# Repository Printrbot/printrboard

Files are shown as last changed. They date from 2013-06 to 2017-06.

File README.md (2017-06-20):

printrboard
===========

Reprap Electronics for the Printrbot

For more info see the Reprap wiki page http://reprap.org/wiki/Printrboard

The BoM with Digikey P/N's is available here: https://goo.gl/G4QnvK

This project, and all of its design files (including the layout), is licensed under the [Creative Commons Attribution-ShareAlike 3.0 Unported](http://creativecommons.org/licenses/by-sa/3.0/) license.

Anyone found to be in violation of this license may not produce or discribute any products using these designs, and will have legal action taken against them.

If you do end up producing boards commercially, a donation of 5% of the retail price or $4 per board would greatly be appreciated. Paypal (lwalkera at ieee.org), or bitcoin 1Cy1JwPiEEVS1RYxfHHFcmJMKbFNrb1Nqd work the best.

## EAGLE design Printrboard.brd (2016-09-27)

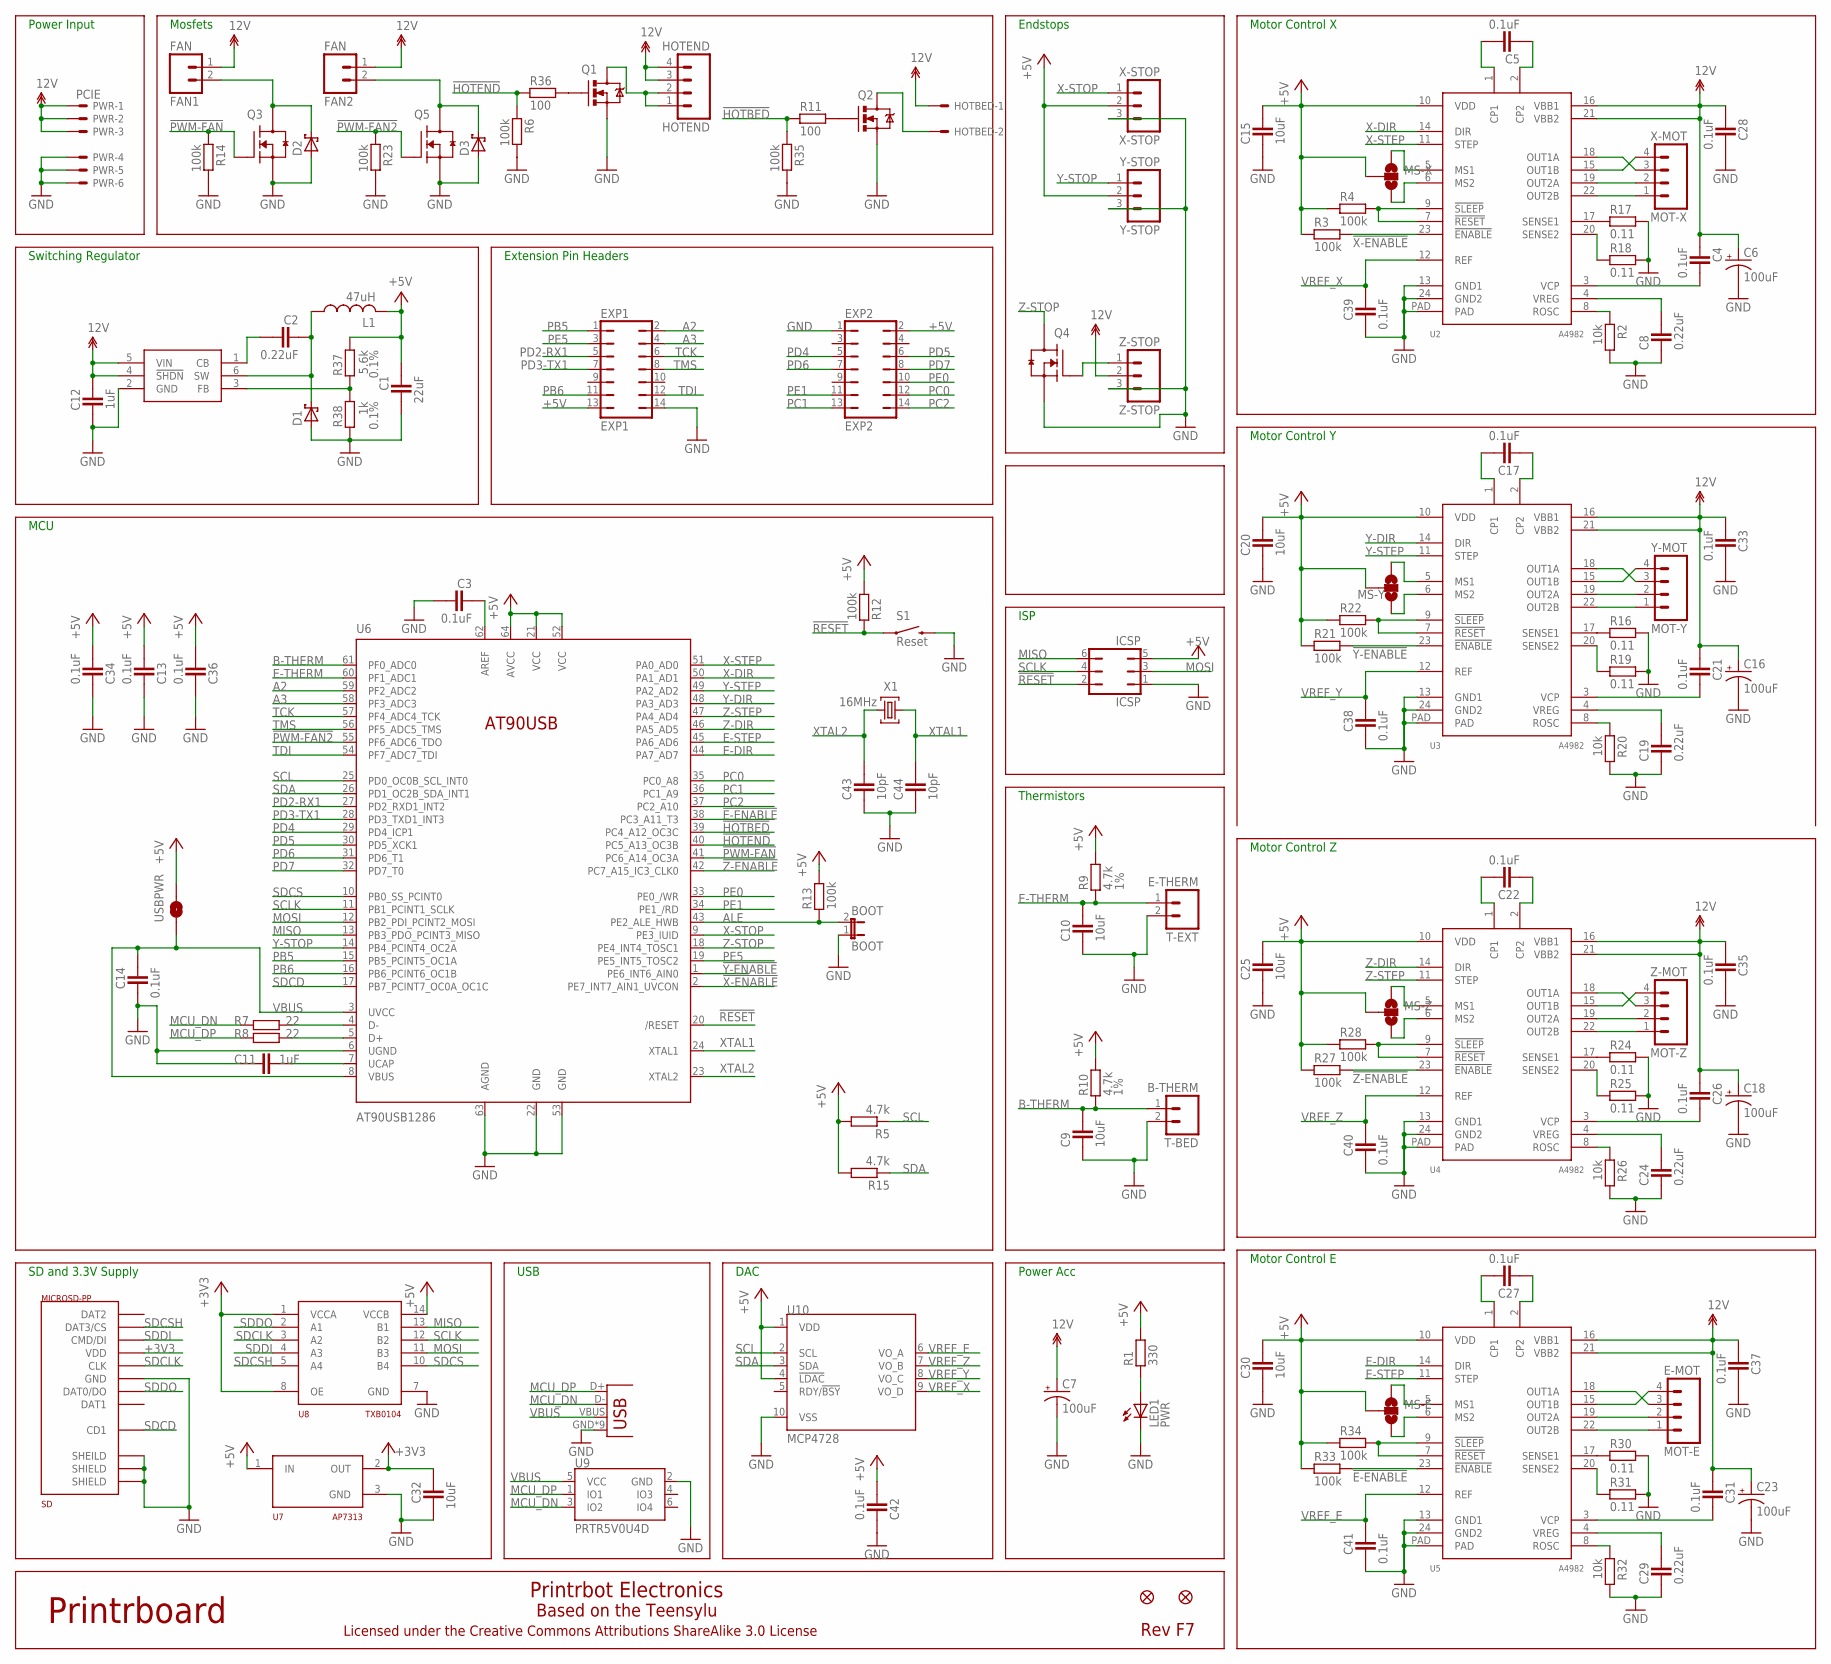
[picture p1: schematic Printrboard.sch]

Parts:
BOOT: BOOT; 1X02
C1: 22uF; CAPC2012X145AN
C2, C8, C19, C24, C29: 0.22uF; CAPC2012X145AN
C3, C4, C5, C13, C14, C17, C21, C22, C26, C27, C28, C31, C33, C34, C35, C36, C37, C38, C39, C40, C41, C42: 0.1uF; CAPC2012X145AN
C6, C7, C16, C18, C23: 100uF; PANASONIC_D
C9, C10, C15, C20, C25, C30, C32: 10uF; CAPC2012X145AN
C11, C12: 1uF; CAPC2012X145AN
C43, C44: 10pF; CAPC2012X145AN
D1, D2, D3: SCH-DIODESMA; SMA
E-MOT: MOT-E; MOLEX-1X4
EXP1: EXP1; JP7Q
EXP2: EXP2; JP7Q
FAN1, FAN2: FAN; 1X02
HOTBED: PHOENIX-2POS-5MM-SCREW; PHOENIX-5MM-2POS
HOTEND: HOTEND; MOLEX-1X4
ICSP: ICSP; JP3Q
JP26, JP33: FIDUCIAL1X2.5; FIDUCIAL-1X2.5
L1: 47uH; SDR1006
LED1: PWR; CHIP-LED0805
MS-E: SOLDERJUMPER_2WAYCONNECTED; SJ_3_CONNECTED
MS-X: SOLDERJUMPER_2WAYCONNECTED; SJ_3_CONNECTED
MS-Y: SOLDERJUMPER_2WAYCONNECTED; SJ_3_CONNECTED
MS-Z: SOLDERJUMPER_2WAYCONNECTED; SJ_3_CONNECTED
PWR: PCIE; 5566-6
Q1, Q2: RFP30N06LE; TO220V
Q3, Q4, Q5: RFP30N06LE; SOT95P280X135-3N
R1: 330; RESC2012X70N
R2, R20, R26, R32: 10k; RESC2012X70N
R3, R4, R6, R12, R13, R14, R21, R22, R23, R27, R28, R33, R34, R35: 100k; RESC2012X70N
R5, R15: 4.7k; RESC2012X70N
R7, R8: 22; RESC2012X70N
R9, R10: 4.7k; RESC2012X70N; TOLERANCE 1%
R11, R36: 100; RESC2012X70N
R16, R17, R18, R19, R24, R25, R30, R31: 0.11; RESC2012X70N
R37: 5.6k; RESC2012X70N; TOLERANCE 0.1%
R38: 1k; RESC2012X70N; TOLERANCE 0.1%
S1: Reset; TACTILE_SWITCH_TALL
SD: MICROSD-PP; USD-101-00660-68-6
T-BED: B-THERM; 1X02
T-EXT: E-THERM; 1X02
U1: LM2841; TSOT6
U2, U3, U4, U5: A4982; TSSOP-24
U6: AT90USB1286; TQFP64-2
U7: AP7313; SOT23C
U8: TXB0104; TSSOP14
U9: PRTR5V0U4D; SOT23-6
U10: MCP4728; MSOP10
USB-M: USB-MICRO-PTH; USB-MICROB-PTH
USBPWR: SOLDERJUMPERNO; SJ_2S-NO
X1: 16MHz; NDK-XTAL
X-MOT: MOT-X; MOLEX-1X4
X-STOP: X-STOP; MOLEX-1X3
Y-MOT: MOT-Y; MOLEX-1X4
Y-STOP: Y-STOP; MOLEX-1X3
Z-MOT: MOT-Z; MOLEX-1X4
Z-STOP: Z-STOP; MOLEX-1X3

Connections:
12V: C4.1, C6.+, C7.+, C12.1, C16.+, C18.+, C21.1, C23.+, C26.1, C28.1, C31.1, C33.1, C35.1, C37.1, FAN1.1, FAN2.1, HOTBED.P$1, HOTEND.3, HOTEND.4, PWR.1, PWR.2, PWR.3, U1.4 (!SHDN), U1.5 (VIN), U2.16 (VBB1), U2.21 (VBB2), U3.16 (VBB1), U3.21 (VBB2), U4.16 (VBB1), U4.21 (VBB2), U5.16 (VBB1), U5.21 (VBB2), Z-STOP.2
!E-ENABLE: R33.2, U5.23 (!ENABLE), U6.38 (PC3_A11_T3)
!HOTBED: R11.1, R35.1, U6.39 (PC4_A12_OC3C)
!HOTEND: R6.1, R36.1, U6.40 (PC5_A13_OC3B)
!PWM-FAN: Q3.1 (G), R14.1, U6.41 (PC6_A14_OC3A)
!PWM-FAN2: Q5.1 (G), R23.1, U6.55 (PF6_ADC6_TDO)
!RESET: ICSP.2, R12.1, S1.A2 (1), U6.20 (/RESET)
!X-ENABLE: R3.2, U2.23 (!ENABLE), U6.2 (PE7_INT7_AIN1_UVCON)
!Y-ENABLE: R21.2, U3.23 (!ENABLE), U6.1 (PE6_INT6_AIN0)
!Z-ENABLE: R27.2, U4.23 (!ENABLE), U6.42 (PC7_A15_IC3_CLK0)
+3V3: C32.1, SD.P$4 (VDD), U7.2 (OUT), U8.1 (VCCA), U8.8 (OE)
+5V: C1.1, C13.2, C15.2, C20.2, C25.2, C30.2, C34.2, C36.2, C42.2, EXP1.13, EXP2.2, ICSP.5, L1.P$2 (2), MS-E.2, MS-X.2, MS-Y.2, MS-Z.2, R1.2, R3.1, R4.1, R5.2, R9.2, R10.2, R12.2, R13.2, R15.2, R21.1, R22.1, R27.1, R28.1, R33.1, R34.1, R37.1, U2.10 (VDD), U3.10 (VDD), U4.10 (VDD), U5.10 (VDD), U6.21 (VCC), U6.52 (VCC), U6.64 (AVCC), U7.1 (IN), U8.14 (VCCB), U10.1 (VDD), U10.4 (!LDAC), USBPWR.2, X-STOP.2, Y-STOP.2
A2: EXP1.2, U6.59 (PF2_ADC2)
A3: EXP1.4, U6.58 (PF3_ADC3)
ALE: BOOT.2, R13.1, U6.43 (PE2_ALE_HWB)
AREF: C3.1, U6.62 (AREF)
B-THERM: C9.2, R10.1, T-BED.1, U6.61 (PF0_ADC0)
E-DIR: U5.14 (DIR), U6.44 (PA7_AD7)
E-STEP: U5.11 (STEP), U6.45 (PA6_AD6)
E-THERM: C10.2, R9.1, T-EXT.1, U6.60 (PF1_ADC1)
GND: BOOT.1, C1.2, C3.2, C6.-, C7.-, C8.1, C9.1, C10.1, C11.1, C12.2, C13.1, C14.2, C15.1, C16.-, C18.-, C19.1, C20.1, C23.-, C24.1, C25.1, C28.2, C29.1, C30.1, C32.2, C33.2, C34.1, C35.2, C36.1, C37.2, C38.2, C39.2, C40.2, C41.2, C42.1, C43.1, C44.1, D1.A, D2.A, D3.A, EXP1.14, EXP2.1, ICSP.1, LED1.C, PWR.4, PWR.5, PWR.6, Q1.3 (S), Q2.3 (S), Q3.2 (S), Q4.2 (S), Q5.2 (S), R2.2, R6.2, R14.2, R16.2, R17.2, R18.2, R19.2, R20.2, R23.2, R24.2, R25.2, R26.2, R30.2, R31.2, R32.2, R35.2, R38.2, S1.B2 (2), SD.GND1 (SHEILD), SD.GND2 (SHIELD), SD.GND3 (SHIELD), SD.P$6 (GND), T-BED.2, T-EXT.2, U1.2 (GND), U2.13 (GND1), U2.24 (GND2), U2.PAD, U3.13 (GND1), U3.24 (GND2), U3.PAD, U4.13 (GND1), U4.24 (GND2), U4.PAD, U5.13 (GND1), U5.24 (GND2), U5.PAD, U6.6 (UGND), U6.22 (GND), U6.53 (GND), U6.63 (AGND), U7.3 (GND), U8.7 (GND), U9.2 (GND), U10.10 (VSS), USB-M.GND, USB-M.GND1 (GND), USB-M.GND2 (GND), USB-M.GND3 (GND), USB-M.GND4 (GND), USB-M.GND5 (GND), USB-M.GND6 (GND), USB-M.GND7 (GND), USB-M.GND8 (GND), X-STOP.3, Y-STOP.3, Z-STOP.3
HOTBED-GND: HOTBED.P$2, Q2.2 (D)
HOTEND-GND: HOTEND.1, HOTEND.2, Q1.2 (D)
MCU_DN: R7.1, U9.3 (IO2), USB-M.D-
MCU_DP: R8.1, U9.1 (IO1), USB-M.D+
MISO: ICSP.6, U6.13 (PB3_PDO_PCINT3_MISO), U8.13 (B1)
MOSI: ICSP.3, U6.12 (PB2_PDI_PCINT2_MOSI), U8.11 (B3)
unnamed: LED1.A, R1.1
unnamed: D2.C, FAN1.2, Q3.3 (D)
unnamed: R7.2, U6.4 (D-)
unnamed: R8.2, U6.5 (D+)
unnamed: Q4.1 (G), Z-STOP.1
unnamed: Q2.1 (G), R11.2
unnamed: D3.C, FAN2.2, Q5.3 (D)
unnamed: C11.2, U6.7 (UCAP)
unnamed: U2.18 (OUT1A), X-MOT.3
unnamed: C5.2, U2.1 (CP1)
unnamed: C5.1, U2.2 (CP2)
unnamed: R2.1, U2.8 (ROSC)
unnamed: R17.1, U2.17 (SENSE1)
unnamed: R18.1, U2.20 (SENSE2)
unnamed: C4.2, U2.3 (VCP)
unnamed: U2.15 (OUT1B), X-MOT.4
unnamed: C8.2, U2.4 (VREG)
unnamed: U2.19 (OUT2A), X-MOT.2
unnamed: R4.2, U2.7 (!RESET), U2.9 (!SLEEP)
unnamed: R37.2, R38.1, U1.3 (FB)
unnamed: U2.22 (OUT2B), X-MOT.1
unnamed: U3.19 (OUT2A), Y-MOT.2
unnamed: U3.22 (OUT2B), Y-MOT.1
unnamed: U3.15 (OUT1B), Y-MOT.4
unnamed: MS-X.1, U2.5 (MS1)
unnamed: MS-X.3, U2.6 (MS2)
unnamed: C17.2, U3.1 (CP1)
unnamed: C17.1, U3.2 (CP2)
unnamed: U3.18 (OUT1A), Y-MOT.3
unnamed: R19.1, U3.20 (SENSE2)
unnamed: R20.1, U3.8 (ROSC)
unnamed: C19.2, U3.4 (VREG)
unnamed: R22.2, U3.7 (!RESET), U3.9 (!SLEEP)
unnamed: C21.2, U3.3 (VCP)
unnamed: R16.1, U3.17 (SENSE1)
unnamed: U4.15 (OUT1B), Z-MOT.4
unnamed: U4.18 (OUT1A), Z-MOT.3
unnamed: U4.19 (OUT2A), Z-MOT.2
unnamed: MS-Y.1, U3.5 (MS1)
unnamed: MS-Y.3, U3.6 (MS2)
unnamed: C22.2, U4.1 (CP1)
unnamed: C22.1, U4.2 (CP2)
unnamed: R24.1, U4.17 (SENSE1)
unnamed: R25.1, U4.20 (SENSE2)
unnamed: R26.1, U4.8 (ROSC)
unnamed: C24.2, U4.4 (VREG)
unnamed: R28.2, U4.7 (!RESET), U4.9 (!SLEEP)
unnamed: C26.2, U4.3 (VCP)
unnamed: U4.22 (OUT2B), Z-MOT.1
unnamed: E-MOT.4, U5.15 (OUT1B)
unnamed: E-MOT.3, U5.18 (OUT1A)
unnamed: E-MOT.2, U5.19 (OUT2A)
unnamed: MS-Z.1, U4.5 (MS1)
unnamed: MS-Z.3, U4.6 (MS2)
unnamed: C27.2, U5.1 (CP1)
unnamed: C27.1, U5.2 (CP2)
unnamed: R30.1, U5.17 (SENSE1)
unnamed: R31.1, U5.20 (SENSE2)
unnamed: R32.1, U5.8 (ROSC)
unnamed: C29.2, U5.4 (VREG)
unnamed: R34.2, U5.7 (!RESET), U5.9 (!SLEEP)
unnamed: C31.2, U5.3 (VCP)
unnamed: E-MOT.1, U5.22 (OUT2B)
unnamed: Q1.1 (G), R36.2
unnamed: MS-E.1, U5.5 (MS1)
unnamed: MS-E.3, U5.6 (MS2)
unnamed: C2.1, D1.C, L1.P$1 (1), U1.6 (SW)
unnamed: C2.2, U1.1 (CB)
PB5: EXP1.1, U6.15 (PB5_PCINT5_OC1A)
PB6: EXP1.11, U6.16 (PB6_PCINT6_OC1B)
PC0: EXP2.12, U6.35 (PC0_A8)
PC1: EXP2.13, U6.36 (PC1_A9)
PC2: EXP2.14, U6.37 (PC2_A10)
PD2-RX1: EXP1.5, U6.27 (PD2_RXD1_INT2)
PD3-TX1: EXP1.7, U6.28 (PD3_TXD1_INT3)
PD4: EXP2.5, U6.29 (PD4_ICP1)
PD5: EXP2.6, U6.30 (PD5_XCK1)
PD6: EXP2.7, U6.31 (PD6_T1)
PD7: EXP2.8, U6.32 (PD7_T0)
PE0: EXP2.10, U6.33 (PE0_/WR)
PE1: EXP2.11, U6.34 (PE1_/RD)
PE5: EXP1.3, U6.19 (PE5_INT5_TOSC2)
SCL: R5.1, U6.25 (PD0_OC0B_SCL_INT0), U10.2 (SCL)
SCLK: ICSP.4, U6.11 (PB1_PCINT1_SCLK), U8.12 (B2)
SDA: R15.1, U6.26 (PD1_OC2B_SDA_INT1), U10.3 (SDA)
SDCD: SD.CD (CD1), U6.17 (PB7_PCINT7_OC0A_OC1C)
SDCLK: SD.P$5 (CLK), U8.3 (A2)
SDCS: U6.10 (PB0_SS_PCINT0), U8.10 (B4)
SDCSH: SD.P$2 (DAT3/CS), U8.5 (A4)
SDDI: SD.P$3 (CMD/DI), U8.4 (A3)
SDDO: SD.P$7 (DAT0/DO), U8.2 (A1)
TCK: EXP1.6, U6.57 (PF4_ADC4_TCK)
TDI: EXP1.12, U6.54 (PF7_ADC7_TDI)
TMS: EXP1.8, U6.56 (PF5_ADC5_TMS)
VBUS: C14.1, U6.3 (UVCC), U6.8 (VBUS), U9.5 (VCC), USB-M.VBUS, USBPWR.1
VREF_E: C41.1, U5.12 (REF), U10.6 (VO_A)
VREF_X: C39.1, U2.12 (REF), U10.9 (VO_D)
VREF_Y: C38.1, U3.12 (REF), U10.8 (VO_C)
VREF_Z: C40.1, U4.12 (REF), U10.7 (VO_B)
X-DIR: U2.14 (DIR), U6.50 (PA1_AD1)
X-STEP: U2.11 (STEP), U6.51 (PA0_AD0)
X-STOP: U6.9 (PE3_IUID), X-STOP.1
XTAL1: C44.2, U6.24 (XTAL1), X1.P$1 (1)
XTAL2: C43.2, U6.23 (XTAL2), X1.P$2 (2)
Y-DIR: U3.14 (DIR), U6.48 (PA3_AD3)
Y-STEP: U3.11 (STEP), U6.49 (PA2_AD2)
Y-STOP: U6.14 (PB4_PCINT4_OC2A), Y-STOP.1
Z-DIR: U4.14 (DIR), U6.46 (PA5_AD5)
Z-STEP: U4.11 (STEP), U6.47 (PA4_AD4)
Z-STOP: Q4.3 (D), U6.18 (PE4_INT4_TOSC1)

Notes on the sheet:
Motor Control X
Motor Control Y
Motor Control Z
Motor Control E
ISP
Thermistors
Endstops
Mosfets
Power Acc
Printrboard
Rev F7
Printrbot Electronics
Licensed under the Creative Commons Attributions ShareAlike 3.0 License
Extension Pin Headers
Switching Regulator
Based on the Teensylu
SD and 3.3V Supply
Power Input
MCU
USB
DAC

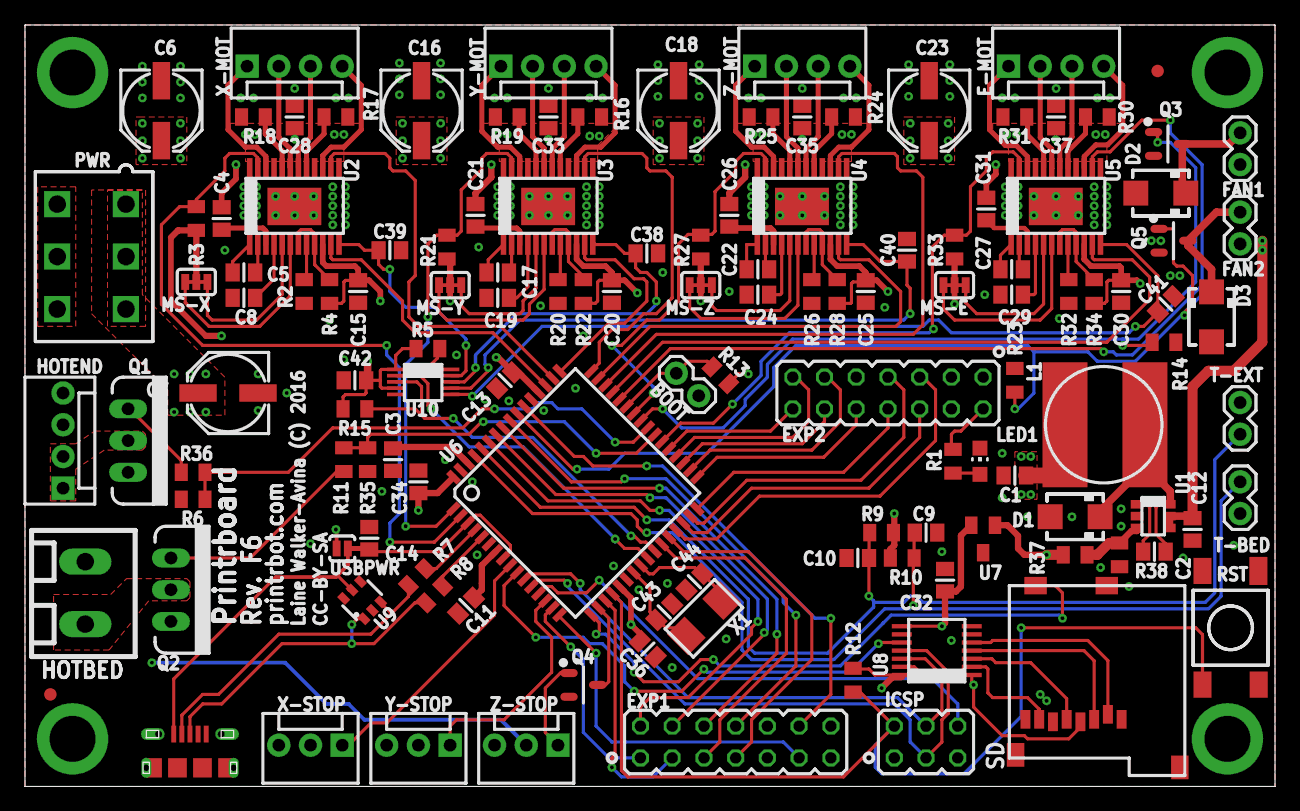
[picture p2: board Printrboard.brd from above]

Board: 4 copper layers, 100.1 x 61.0 mm, 130 parts (0 on the bottom side), 137 nets.

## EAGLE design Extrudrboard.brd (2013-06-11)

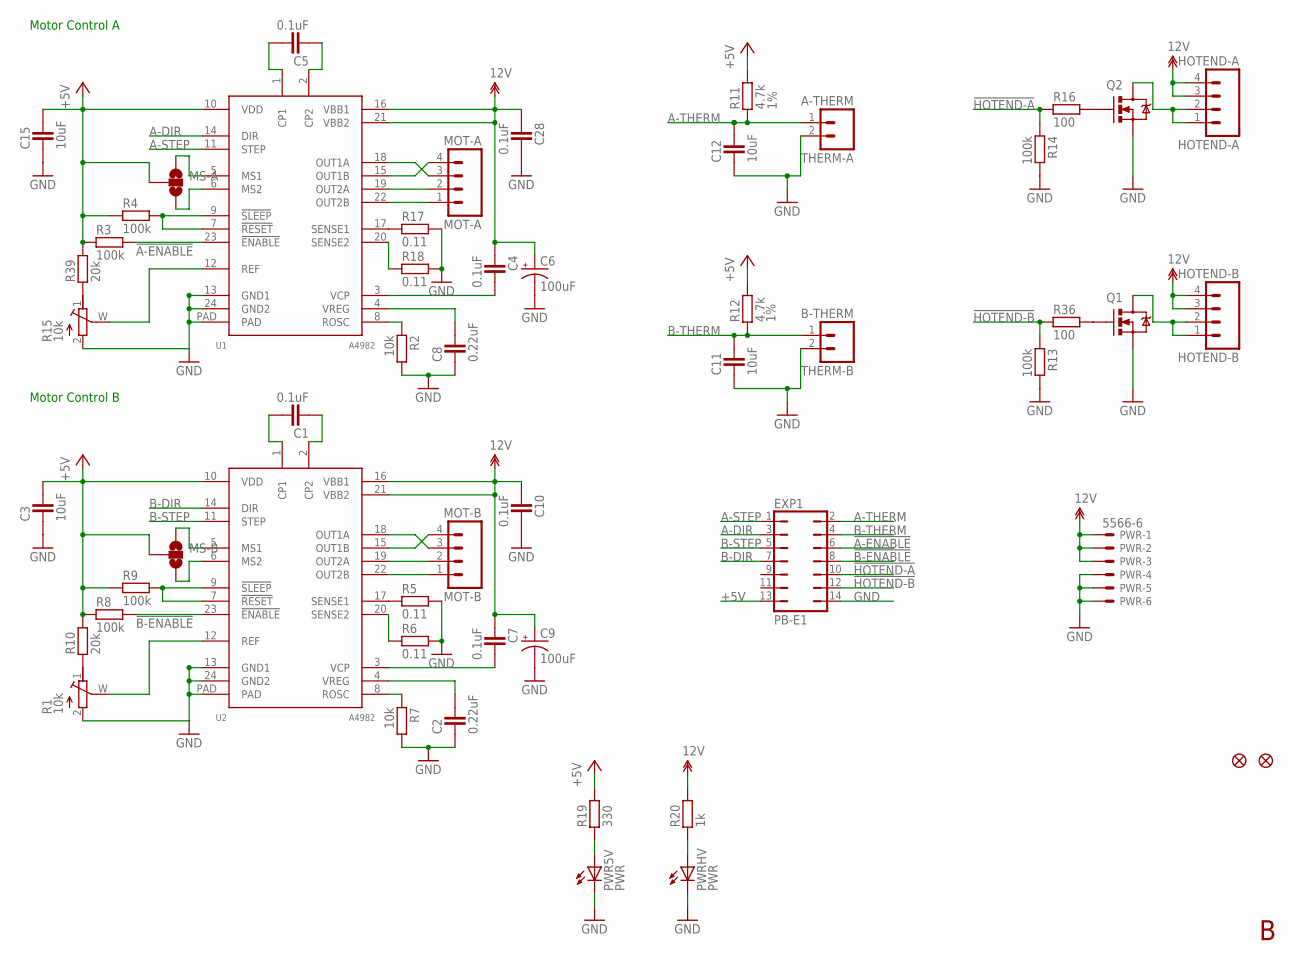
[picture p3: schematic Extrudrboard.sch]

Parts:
C1, C4, C5, C7, C10, C28: 0.1uF; CAPC2012X145AN
C2, C8: 0.22uF; CAPC2012X145AN
C3, C11, C12, C15: 10uF; CAPC2012X145AN
C6, C9: 100uF; PANASONIC_D
EXP1: PB-E1; JP7Q
HOTEND-A: HOTEND-A; MOLEX-1X4
HOTEND-B: HOTEND-B; MOLEX-1X4
JP1, JP2: FIDUCIAL1X2.5; FIDUCIAL-1X2.5
MOT-A: MOT-A; MOLEX-1X4
MOT-B: MOT-B; MOLEX-1X4
MS-A: SOLDERJUMPER_2WAYCONNECTED; SJ_3_CONNECTED
MS-B: SOLDERJUMPER_2WAYCONNECTED; SJ_3_CONNECTED
PWR: 5566-6
PWR5V: PWR; CHIP-LED0805
PWRHV: PWR; CHIP-LED0805
Q1, Q2: MOSFET-NCHANNELPTH2; TO220V
R1, R15: 10k; RTRIM-ST4ETB
R2, R7: 10k; RESC2012X70N
R3, R4, R8, R9, R13, R14: 100k; RESC2012X70N
R5, R6, R17, R18: 0.11; RESC2012X70N
R10, R39: 20k; RESC2012X70N
R11, R12: 4.7k; RESC2012X70N; TOLERANCE 1%
R16, R36: 100; RESC2012X70N
R19: 330; RESC2012X70N
R20: 1k; RESC2012X70N
THERM-A: A-THERM; 1X02
THERM-B: B-THERM; 1X02
U1, U2: A4982; TSSOP-24

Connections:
12V: C4.1, C6.+, C7.1, C9.+, C10.1, C28.1, HOTEND-A.3, HOTEND-A.4, HOTEND-B.3, HOTEND-B.4, PWR.1, PWR.2, PWR.3, R20.2, U1.16 (VBB1), U1.21 (VBB2), U2.16 (VBB1), U2.21 (VBB2)
!A-ENABLE: EXP1.6, R3.2, U1.23 (!ENABLE)
!B-ENABLE: EXP1.8, R8.2, U2.23 (!ENABLE)
!HOTEND-A: EXP1.10, R14.1, R16.1
!HOTEND-B: EXP1.12, R13.1, R36.1
+5V: C3.2, C15.2, EXP1.13, MS-A.2, MS-B.2, R3.1, R4.1, R8.1, R9.1, R10.2, R11.2, R12.2, R19.2, R39.2, U1.10 (VDD), U2.10 (VDD)
A-DIR: EXP1.3, U1.14 (DIR)
A-STEP: EXP1.1, U1.11 (STEP)
A-THERM: C12.2, EXP1.2, R11.1, THERM-A.1
B-DIR: EXP1.7, U2.14 (DIR)
B-STEP: EXP1.5, U2.11 (STEP)
B-THERM: C11.2, EXP1.4, R12.1, THERM-B.1
GND: C2.1, C3.1, C6.-, C8.1, C9.-, C10.2, C11.1, C12.1, C15.1, C28.2, EXP1.14, PWR.4, PWR.5, PWR.6, PWR5V.C, PWRHV.C, Q1.3 (S), Q2.3 (S), R1.2 (E), R2.2, R5.2, R6.2, R7.2, R13.2, R14.2, R15.2 (E), R17.2, R18.2, THERM-A.2, THERM-B.2, U1.13 (GND1), U1.24 (GND2), U1.PAD, U2.13 (GND1), U2.24 (GND2), U2.PAD
HOTENDA-GND: HOTEND-A.1, HOTEND-A.2, Q2.2 (D)
HOTENDB-GND: HOTEND-B.1, HOTEND-B.2, Q1.2 (D)
unnamed: C1.2, U2.1 (CP1)
unnamed: C1.1, U2.2 (CP2)
unnamed: R5.1, U2.17 (SENSE1)
unnamed: R6.1, U2.20 (SENSE2)
unnamed: R1.W (S), U2.12 (REF)
unnamed: R7.1, U2.8 (ROSC)
unnamed: C2.2, U2.4 (VREG)
unnamed: R9.2, U2.7 (!RESET), U2.9 (!SLEEP)
unnamed: C7.2, U2.3 (VCP)
unnamed: MOT-A.3, U1.18 (OUT1A)
unnamed: C5.2, U1.1 (CP1)
unnamed: C5.1, U1.2 (CP2)
unnamed: R2.1, U1.8 (ROSC)
unnamed: R17.1, U1.17 (SENSE1)
unnamed: R18.1, U1.20 (SENSE2)
unnamed: C4.2, U1.3 (VCP)
unnamed: MOT-A.4, U1.15 (OUT1B)
unnamed: R15.W (S), U1.12 (REF)
unnamed: C8.2, U1.4 (VREG)
unnamed: MOT-A.2, U1.19 (OUT2A)
unnamed: R4.2, U1.7 (!RESET), U1.9 (!SLEEP)
unnamed: MS-B.1, U2.5 (MS1)
unnamed: MOT-A.1, U1.22 (OUT2B)
unnamed: MS-B.3, U2.6 (MS2)
unnamed: MOT-B.3, U2.18 (OUT1A)
unnamed: MOT-B.4, U2.15 (OUT1B)
unnamed: MS-A.1, U1.5 (MS1)
unnamed: MS-A.3, U1.6 (MS2)
unnamed: MOT-B.2, U2.19 (OUT2A)
unnamed: MOT-B.1, U2.22 (OUT2B)
unnamed: R1.1 (A), R10.1
unnamed: Q2.1 (G), R16.2
unnamed: PWR5V.A, R19.1
unnamed: PWRHV.A, R20.1
unnamed: R15.1 (A), R39.1
unnamed: Q1.1 (G), R36.2

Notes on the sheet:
Motor Control A
Motor Control B

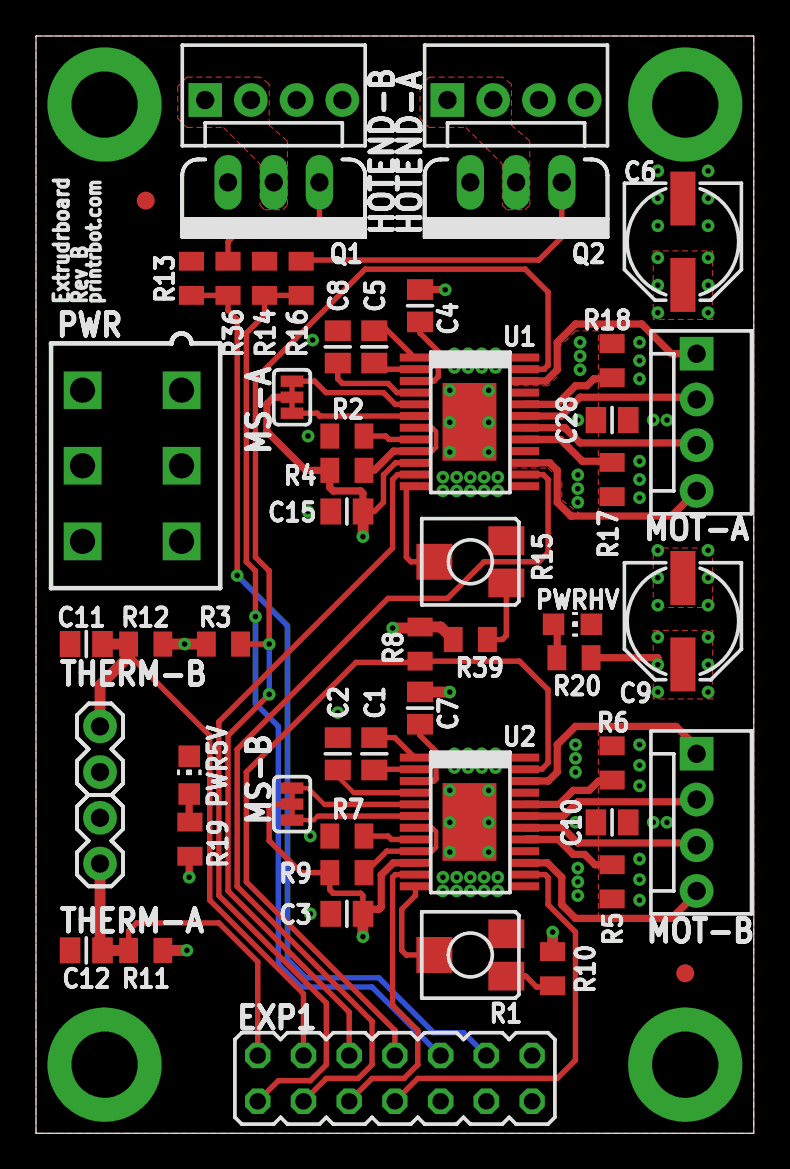
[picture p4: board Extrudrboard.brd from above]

Board: 4 copper layers, 39.9 x 61.0 mm, 54 parts (0 on the bottom side), 51 nets.

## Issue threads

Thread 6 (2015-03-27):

Add BOM to repo

jbryson3, 2015-03-27:
It would be helpful to track changes in the actual parts used. For instance, I'm looking at the current BOM for the F4 board and it shows Q4 as a BJT, where on my Printrbot F4 board, I see a FET. Not sure what changed and when, especially since the boards are the same version.

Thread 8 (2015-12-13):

Add feature to allow control of hotend fan

PxT, 2015-12-13:
It would be good to have software / firmware control of the always-on hotend fan.  Currently these are just wired to constant power on the board but a controllable pin that cuts power when the hotend is below a safe threshold would be better.  That way when a print is complete and the hotend cools completely the fan could shut off automatically, reducing noise and extending the life of the fan.

Not sure if this requires a hardware redesign or not.  Would definitely require a corresponding firmware modification.  There is precedent for this feature in Repetier firmware w/ RAMBO boards.

PxT, 2015-12-13:
Further discussion here: http://www.printrbottalk.com/forum/viewtopic.php?f=21&t=10508&p=67897&hilit=fan+mosfet#p67897

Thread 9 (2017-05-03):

Charge pump capacitors on A4982's sing

jetty840, 2017-05-03:
The charge pump 0.1uF capacitors on the CP1/CP2 pins on the A4982 sing emitting a high pitch sound which can be detected by and is irritating to younger users, approximately 12-16KHz.

The charge pump operates at 52KHz, with a superimposed waveform of approximately 6-8Khz at 8V peak to peak.  This causes the piezo material in the Y5V capacitor to emit sound due to the piezo electric effect at the fundamental and resonate at the 1st harmonic.  Frequency can vary slightly from driver to driver according to manufacturing tolerances in the A4982 charge pump circuitry.

A 14dB improvement can be achieved by replacing these 4 caps with a X7R Kemet P/N  C0805C104K1RACTU.

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

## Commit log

2011-11-23 Fix some thermal, and angle errors. Add some additional caps on Vbb rail. More work on the silkscreen
    [Printrboard.brd, Printrboard.sch]
2011-11-25 Add solder jumpers and move placement artwork for the Allegro package to tPlace
2011-11-25 Change to using solder jumpers for the microstepping selection
    [Printrboard.brd, Printrboard.sch]
2011-11-30 Change thermal vias for the stepper driver, reduce paste area on drivers to 75%, make edge clearance 20 mils, and bring Vbb ceramic cap to top side
    [Printrboard.brd, Printrboard.sch]
2011-11-30 Tweak the position of the motor traces
    [Printrboard.brd]
2011-12-03 Copy level translator and LDO from SD adapter project in prep for 5V conversion
2011-12-03 Add resistors on all the Vref pots to allow for 5V change, and cleanup the silkscreen layers
    [Printrboard.brd, Printrboard.sch]
2011-12-10 Change logic voltage to 5V, add translation circuitry for SD, move to 4-layer design, and cleanup some packages
    [Printrboard.brd, Printrboard.sch]
2011-12-11 Tweak the board to pass 4pcb.com DFM
    [Printrboard.brd]
2011-12-16 Convert files to EAGLE 6
    [Printrboard.brd, Printrboard.sch]
2012-01-02 Fix angle errors caused by 6.0 conversion, add more decoupling caps to MCU, and modify some routing
    [Printrboard.brd, Printrboard.sch]
2012-01-16 Change some caps around, add a solder jumper for USB sourced 5V, and modify silkscreen for production
    [Printrboard.brd, Printrboard.sch]
2012-01-19 Add extra solder pads for USB connector, and square up mounting holes
    [Printrboard.brd, Printrboard.sch]
2012-04-03 Fixes for Rev C
    -Made all mounting holes the same size
    -Changed package for stepper solder jumpers to be connected by copper by
    default
    [Printrboard.brd, Printrboard.sch]
2012-04-05 Board tweaks for rev D
    Move endstop connectors apart for more clearance and move the labels for
    the heaters around so they're easier to see
    [Printrboard.brd, Printrboard.sch]
2012-05-03 Make resonator pad larger to accomodate both available pacakages, and change polarity of BOOT jumper
    [Printrboard.brd, Printrboard.sch]
2012-05-28 Small layout tweaks for Rev D
    * Moved temp inputs closer to center of board and repositioned label so that
    they can be seen.
    * Gave the bottom expansion connector a little room by moving the ICSP port over a bit
    * Moved the cap next to the resonator a little farther away from each other
    [Printrboard.brd]
2012-12-31 Add in 6-pin PCIe power connector
2012-12-31 Fix values for sense resistors to match BoM
    [Printrboard.brd, Printrboard.sch]
2013-06-11 Add gerber stuff to gitignore
2013-06-11 Add files for Extrudrboard Rev B
    [Extrudrboard.brd, Extrudrboard.sch]
2013-10-23 Update files for Rev F
    Changed heatbed connector to 5mm pitch screw terminal
    Removed E-STOP connector
    Changed Y-STOP pin
    Moved former Y-STOP pin to SD interface to fix a limitation of the SPI ctlr
    Added I2C connector
    Replaced trimpots with 4-channel I2C DAC
    Added polyfuse and reverse protection diode to fan circuit
    Added more empty space around fan connector
    Made ICSP and EXP1 connector pins share a 0.1" grid
    Removed reset signal from EXP1, and replaced it with GPIO
    Changed input PWR connector to a 6-pin one from the same family
    Removed stop layer from several vias for future bed-of-nails tester
    Change to through-hole mount microUSB connector
    Added USB TVS diode pack to protect USB controlle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
    [Printrboard.brd, Printrboard.sch]
2013-10-31 Manufacturability changes
    Added some pin 1 indicators
    Added test point for VBUS signal
    [Printrboard.brd, Printrboard.sch]
2014-05-22 Minor schematic changes
    [Printrboard.sch]
2014-06-03 Redraw USB connector for manufacturability
    [Printrboard.brd, Printrboard.sch]
2014-07-10 Add in voltage selection and input buffering for the Z-stop
    [Printrboard.brd, Printrboard.sch]
2015-01-15 Bump rev to F5 and update copyright date
    [Printrboard.brd, Printrboard.sch]
2016-06-23 Rev F6
    Add second Fan port
    Add optional USB-B footprint
    Remove polyswitch
    Change to push-push microSD socket
    [Printrboard.brd, Printrboard.sch]
2016-09-27 Add in changes requested by PBHQ
    [Printrboard.brd, Printrboard.sch]
2017-06-20 Update README.md with better link to BoM

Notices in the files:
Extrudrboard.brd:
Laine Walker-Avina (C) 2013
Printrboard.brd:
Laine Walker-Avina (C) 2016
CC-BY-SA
